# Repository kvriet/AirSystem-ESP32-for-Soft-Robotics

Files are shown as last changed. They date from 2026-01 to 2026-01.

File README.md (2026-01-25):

# AirSystem for Soft Robotics
Modular Air System for Soft Robotics using ESP32\
Designed and created by [C.M. van Riet](https://research.tue.nl/en/persons/cm-katrien-van-riet) - Jan 2026\
With thanks to d.search at Eindhoven University of Technology for their guidance.\
Special thanks to Geert van den Boomen for checking the schematics and debugging the circuits.

## The system
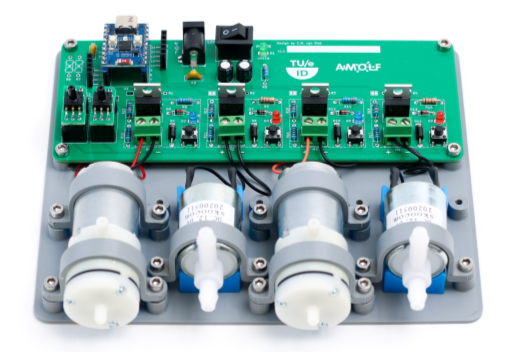
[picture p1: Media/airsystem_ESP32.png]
Example application


**AirSystem-ESP32** was designed as a low-cost way to rapidly prototype with air, costing roughly €60 for the entire system. AirSystem consists of 1 controller, 4 pneumatic components (pumps and valves), and 2 pressure sensors. Through a 12V power brick, the board provides 12V power and as such, any pump or solenoid that requires 12V power can be attached to the board. 

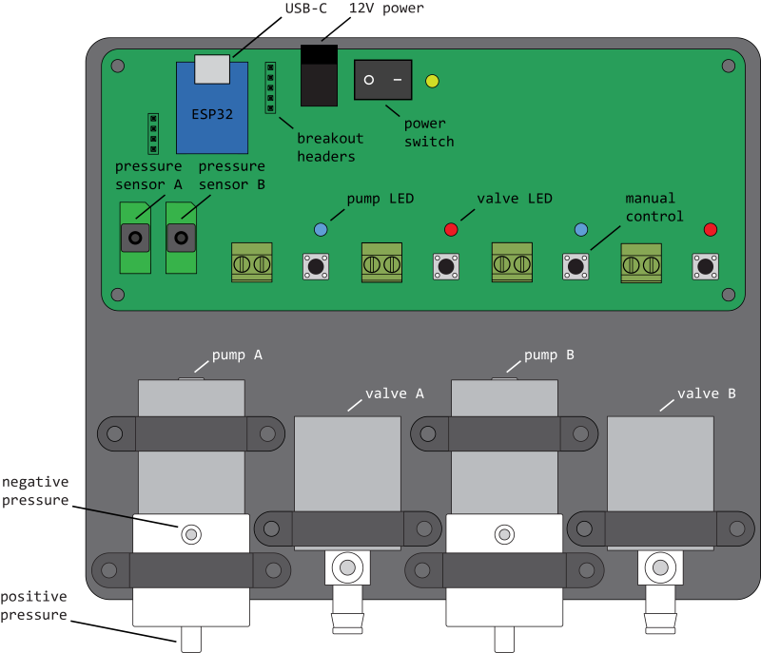
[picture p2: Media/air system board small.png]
System overview


### Pneumatic Components
For the pneumatic board, easy-to-find components are used:
1. Pump 370A, 12V, 3.2LPM
2. Solenoid valve Skoocom SC0829GW, 12V
3. MCP-H10 pressure sensor, 0-200kPa, 3.3V

### Manual
A manual for AirSystem describes in detail how the system works and how the Arduino library can be installed: [AirSystem Manual](https://github.com/kvriet/AirSystem-ESP32-for-Soft-Robotics/blob/main/Air%20System%20manual%20pcb%20v1.3.pdf)
Users are free to connect the sensor, pump, and valve to their inflatables as desired. Example Arduino sketches are provided that work well with the board to control inflatables.

## Arduino Library
The system is controlled by a Waveshare ESP32-C3-Zero and can be programmed through the Arduino IDE with a custom library: [AirSystem](https://github.com/kvriet/AirSystem-ESP32-for-Soft-Robotics/blob/main/AirSystem-ESP.zip) This folder should be unzipped and placed in the libraries folder of the Arduino folder, or imported (zipped) as a library in the Arduino IDE. Select the XIAO_ESP32C3 board to upload sketches to the board.

The library comes with 7 examples that showcase the abilities of **AirSystem**:
  1. Manual control
  2. Pressure reading
  3. Pump control
  4. Valve control
  5. Pump control without delay
  6. Other configurations
  7. Object arrays

## Schematics and KiCAD Files
The schematics for this project and the KiCAD files can be found here: [KiCAD folder](https://github.com/kvriet/AirSystem-for-Soft-Robotics/tree/main/KiCAD).

## 3D Printing Files
The STLs for this project can be found here: [Design Files](https://github.com/kvriet/AirSystem-ESP32-for-Soft-Robotics/tree/main/Design%20files).
- The prints will fit most regular printers and can be printed out of PLA, 0.3 layer height, 4 perimeters (walls), 20% infill. The cushions for the pumps and solenoids are printed in TPU. These cushions can be replaced with some sponge (simple kitchen sponges work well) if TPU printing is not an option.
- To minimise vibrations and prevent the cases from sliding around on a hard surface, 6mm silicone feet can be added to the bottom of the base.

The screws needed for these cases are:
- 4x M3x5 for the PCB 
- 12x M3x10 for the clamps (or 16x M3x10 depending on the configuration)

## Limitations
- The Skoocom solenoid valve is able to remain closed up to pressures of 100kPa, whereas the pump is able to deliver 150kPa. This means the valve will start leaking at pressures over 100kPa. In practice, this is not a major issue, as our projects rarely need pressures of over 100kPa (usually maxing out at 50kPa for haptic purposes). However, this overpressure might reduce valve longevity in the long run. In the future, a higher-pressure solenoid valve could be found, or a pump could be found that delivers max 100kPa. This would also allow for a lower-range pressure sensor to be used, the MCP-H10 0-100kPa, 3.3V. Switching to the 0-100kPa sensor would also double pressure measuring resolution.
- Currently no PID has been implemented in the library. As many inflatables or the tubing used are somewhat elastic, I have found that setting a target pressure (feedback loop sensor reading to pump power) is enough to achieve that pressure with a minimal offset. However, for more high-end applications, PID should be implemented.
- The Skoocom solenoid valve is not proportional. It is just open/closed. This means that controller deflation is a challenge. This can be worked around by turning on the pump simultaneously to opening the valve to reduce the air flowing out. Additionally, a resistor (very thin tube) could be connected to the valve outlet to reduce airflow out of the system. However, such a resistor also slows down response times when air does need to evacuate the system quickly. This is a trade-off for how cheap this entire system is.

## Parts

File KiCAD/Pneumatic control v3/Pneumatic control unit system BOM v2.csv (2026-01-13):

Reference | Value | Datasheet | Footprint | Qty | DNP | Katrien will provide
C1,C4,C5,C6,C7,C8 | 100nF | ~ | Capacitor_THT:C_Rect_L7.2mm_W2.5mm_P5.00mm_FKS2_FKP2_MKS2_MKP2 | 6 |  | no
C2,C3 | 100uF | ~ | Capacitor_THT:CP_Radial_D6.3mm_P2.50mm | 2 |  | no
D1,D7 | LED_Blue | ~ | LED_THT:LED_D3.0mm | 2 |  | no
D2,D8 | LED_Red | ~ | LED_THT:LED_D3.0mm | 2 |  | no
D3,D4,D9,D10 | 1N4001 | http://www.vishay.com/docs/88503/1n4001.pdf | Diode_THT:D_DO-41_SOD81_P10.16mm_Horizontal | 4 |  | no
D5,D6,D11,D12 | 1N4148 | https://assets.nexperia.com/documents/data-sheet/1N4148_1N4448.pdf | Diode_THT:D_DO-35_SOD27_P7.62mm_Horizontal | 4 |  | no
D13 | LED_Small | ~ | LED_THT:LED_D3.0mm | 1 |  | no
J1 | Barrel_Jack | https://www.tinytronics.nl/en/cables-and-connectors/connectors/dc-jack/dc-jack-plastic-5.5mm-female | Connector_BarrelJack:BarrelJack_Horizontal | 1 |  | yes
J2,J3 | Conn | ~ | -- mixed values -- | 2 |  | no
J4 | GND | ~ | TestPoint:TestPoint_Loop_D2.50mm_Drill1.0mm | 1 | DNP | no
JP1,JP2,JP3,JP4,JP5,JP6 | jumper | ~ | Jumper:SolderJumper-2_P1.3mm_Bridged_Pad1.0x1.5mm | 6 |  | no
M1,M3 | Pump | ~ | TerminalBlock_Phoenix:TerminalBlock_Phoenix_MKDS-1,5-2_1x02_P5.00mm_Horizontal | 2 |  | yes
M2,M4 | Valve | ~ | TerminalBlock_Phoenix:TerminalBlock_Phoenix_MKDS-1,5-2_1x02_P5.00mm_Horizontal | 2 |  | yes
Q1,Q2,Q3,Q4 | IRLB8743PBF | https://www.infineon.com/assets/row/public/documents/24/49/infineon-irlr8743-datasheet-en.pdf | Package_TO_SOT_THT:TO-220-3_Vertical | 4 |  | no
R1,R2,R3,R4 | 1k | ~ | Resistor_THT:R_Axial_DIN0207_L6.3mm_D2.5mm_P10.16mm_Horizontal | 4 | DNP | no
R5,R11,R17 | 3k3 | ~ | Resistor_THT:R_Axial_DIN0207_L6.3mm_D2.5mm_P10.16mm_Horizontal | 3 |  | no
R6,R12 | 1k2 | ~ | Resistor_THT:R_Axial_DIN0207_L6.3mm_D2.5mm_P10.16mm_Horizontal | 2 |  | no
R7,R8,R13,R14 | 1k | ~ | Resistor_THT:R_Axial_DIN0207_L6.3mm_D2.5mm_P10.16mm_Horizontal | 4 |  | no
R9,R10,R15,R16 | 100k | ~ | Resistor_THT:R_Axial_DIN0207_L6.3mm_D2.5mm_P10.16mm_Horizontal | 4 |  | no
SW1 | SW_SPST | https://www.tinytronics.nl/en/switches/manual-switches/rocker-switches/standaard-built-in-rocker-switch-small | Library:SW_rocker_switch_small | 1 |  | yes
SW2,SW3,SW4,SW5 | SW_Push | ~ | Button_Switch_THT:SW_PUSH_6mm | 4 |  | no
U1,U2 | ~ |  | Library:MCP_H10_breakout | 2 |  | yes
U3 | ESP32-C3-Zero |  | ESP32-C3-Zero | 1 |  | yes

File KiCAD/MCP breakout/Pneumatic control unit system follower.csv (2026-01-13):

Reference | Value | Datasheet | Footprint | Qty | DNP
C1,C2,C3,C4,C7,C8,C11 | 100nF | ~ | Capacitor_SMD:C_0603_1608Metric_Pad1.08x0.95mm_HandSolder | 7
C5,C6,C9,C10 | 100uF | ~ | Capacitor_THT:CP_Radial_D6.3mm_P2.50mm | 4
D1,D3 | LED_Small | ~ | Diode_SMD:D_0805_2012Metric_Pad1.15x1.40mm_HandSolder | 2
D2,D4 | 1N4007 | http://www.vishay.com/docs/88503/1n4001.pdf | Diode_SMD:D_SMA_Handsoldering | 2
D5,D6 | 1N4148 | https://assets.nexperia.com/documents/data-sheet/1N4148_1N4448.pdf | Diode_SMD:D_MiniMELF_Handsoldering | 2
J1 | unit_1 | https://www.tinytronics.nl/en/cables-and-connectors/connectors/jst-compatible/jst-xh-6p-compatible-pcb-connector-male-90 | Library:JST_XH_S6B-XH-A-1_1x06_P2.50mm_Horizontal_5mm | 1
M1,M2 | Pump | ~ | TerminalBlock_Phoenix:TerminalBlock_Phoenix_MPT-0,5-2-2.54_1x02_P2.54mm_Horizontal | 2
Q1,Q2 | AO3400A | http://www.aosmd.com/pdfs/datasheet/AO3400A.pdf | Package_TO_SOT_SMD:SOT-23 | 2
R1,R4 | 680R | ~ | Resistor_SMD:R_0603_1608Metric_Pad0.98x0.95mm_HandSolder | 2
R2,R5 | 330R | ~ | Resistor_SMD:R_0603_1608Metric_Pad0.98x0.95mm_HandSolder | 2
R3,R6 | 100k | ~ | Resistor_SMD:R_0603_1608Metric_Pad0.98x0.95mm_HandSolder | 2
SW1,SW2 | SW_Push | ~ | Button_Switch_THT:SW_PUSH_6mm | 2
U1 | ~ |  | Library:MCP-H10 | 1

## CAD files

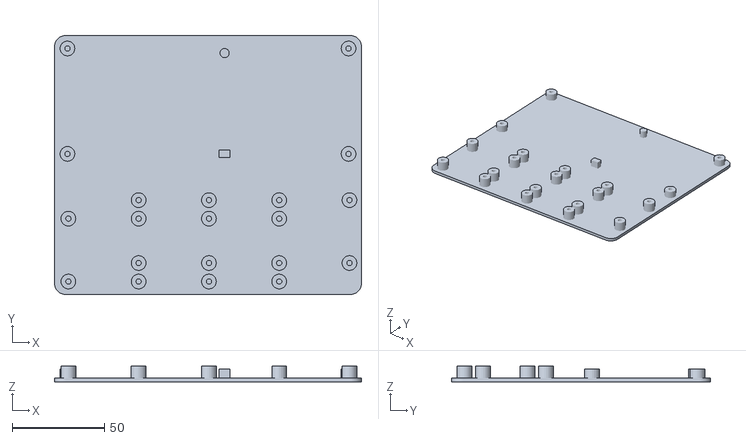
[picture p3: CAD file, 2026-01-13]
Design files/pcb base v2.stl
166.0 x 140.0 x 8.50

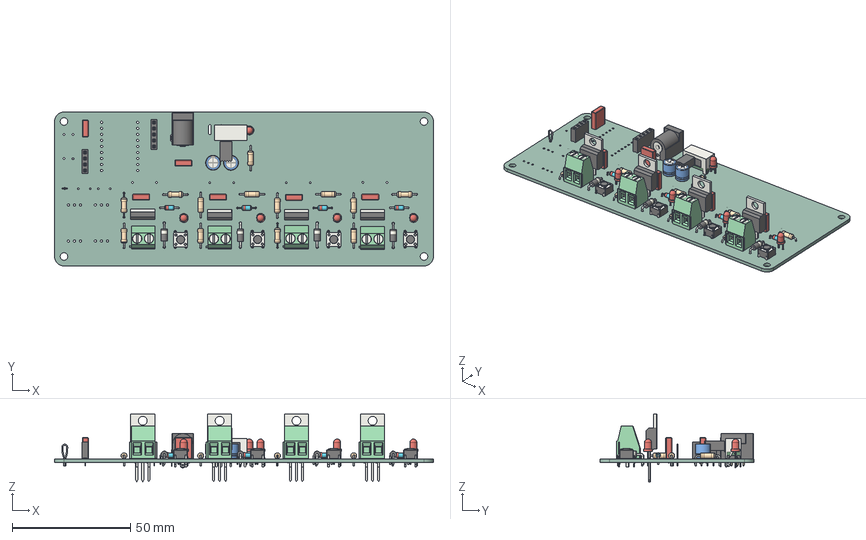
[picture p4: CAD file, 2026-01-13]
KiCAD/Pneumatic control v3/control unit v3.step
160.0 x 65.0 x 28.5 mm
C_Rect_L72mm_W25mm_P500mm_FKS2_FKP2_MKS2_MKP2 x 6
R_Axial_DIN0207_L63mm_D25mm_P1016mm_Horizontal x 13
LED_D3.0mm x 5
SW_PUSH_6mm x 4
PinSocket_1x04_P254mm_Vertical
D_DO-41_SOD81_P10.16mm_Horizontal x 4
TO-220-3_Vertical x 4
PinSocket_1x05_P254mm_Vertical
TerminalBlock_Phoenix_MKDS_15_2_1x02_P500mm_Horizontal x 4
D_DO-35_SOD27_P7.62mm_Horizontal x 4
CP_Radial_D63mm_P250mm x 2
SW_E-Switch_EG1224_SPDT_Angled
BarrelJack_Horizontal
TestPoint_Loop_D2.50mm_Drill1.0mm
Pneumatic control unit system_PCB

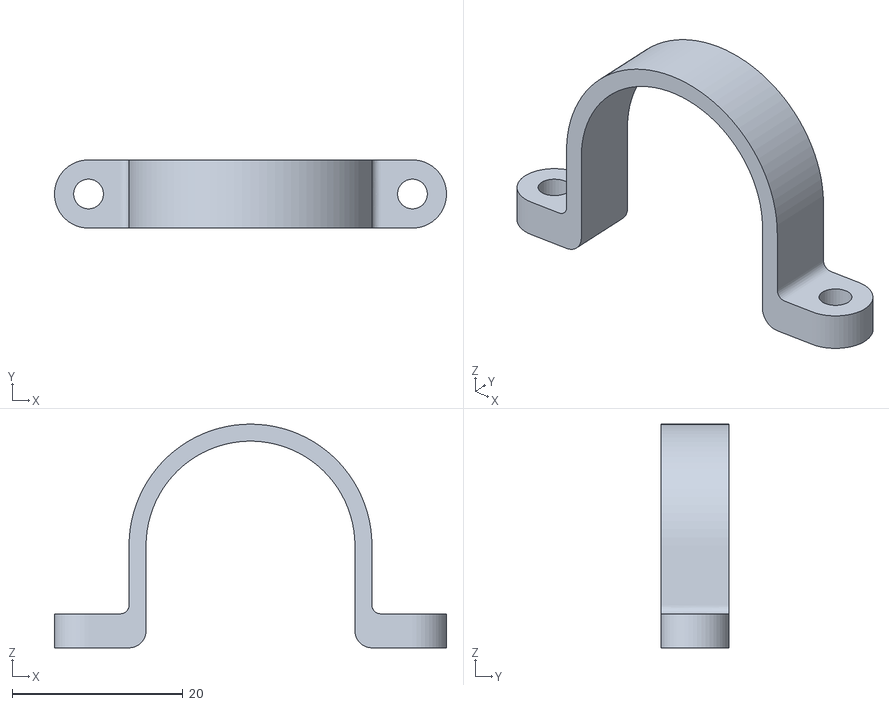
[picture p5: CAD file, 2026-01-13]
Design files/clamp small v5.stl
46.0 x 8.00 x 26.2

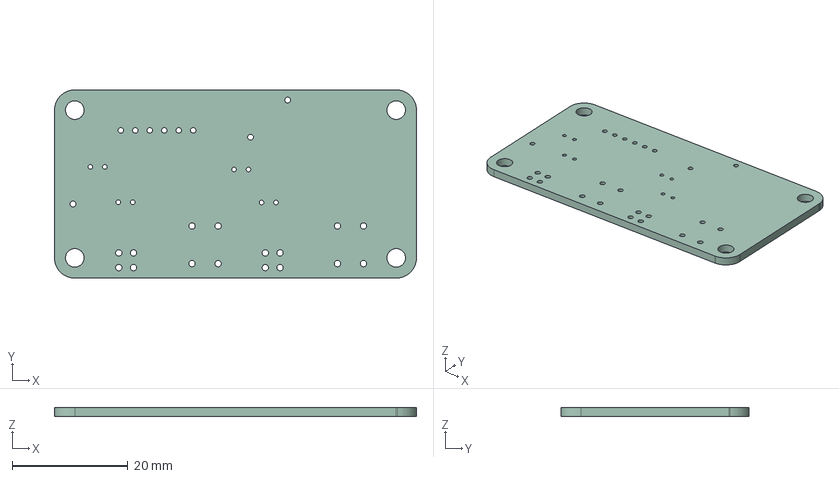
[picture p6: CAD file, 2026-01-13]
KiCAD/MCP breakout/Pneumatic control unit system broad.step
62.5 x 32.5 x 1.60 mm

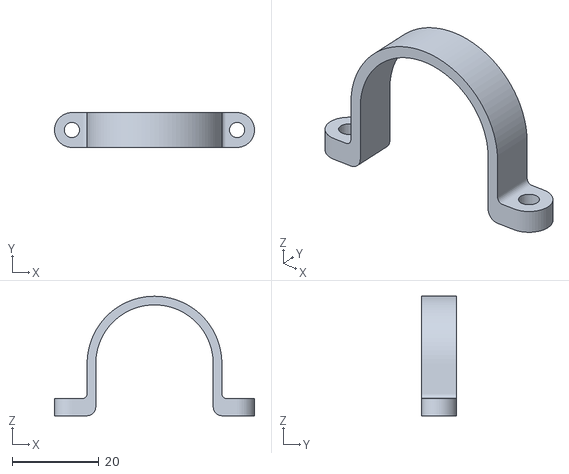
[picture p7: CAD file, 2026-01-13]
Design files/clamp big v5.stl
46.0 x 8.00 x 27.5

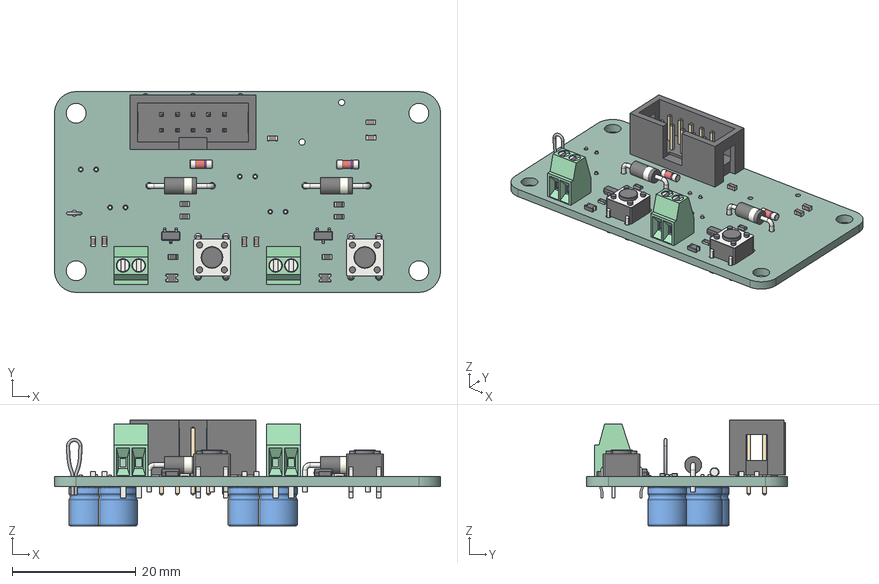
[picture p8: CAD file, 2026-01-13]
KiCAD/MCP breakout/follower v8.2.step
62.5 x 32.5 x 17.1 mm
R_0603_1608Metric x 6
D_MiniMELF_Standard x 2
D_DO-41_SOD81_P10.16mm_Horizontal x 2
SW_PUSH_6mm x 2
TestPoint_Loop_D2.50mm_Drill1.0mm
C_0603_1608Metric x 7
IDC_Header_2x05_P254mm_Vertical
TerminalBlock_Phoenix_MPT_05_2_254_1x02_P254mm_Horizontal x 2
SOT_23 x 2
D_0805 x 2
CP_Radial_D63mm_P250mm x 4
Pneumatic control unit system_PCB

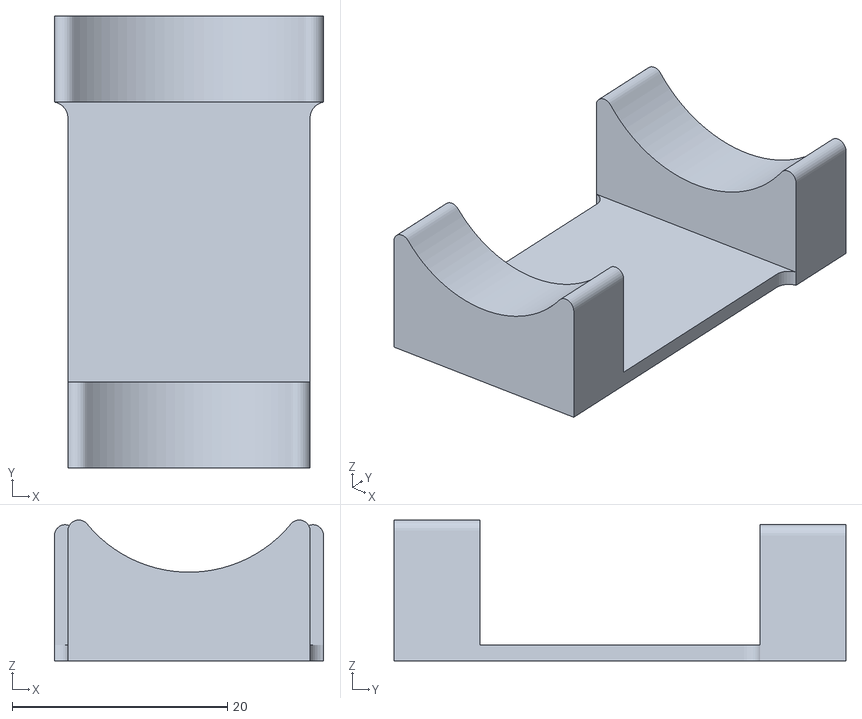
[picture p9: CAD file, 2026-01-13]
Design files/cushion connected v3.stl
25.0 x 42.0 x 13.1

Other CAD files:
KiCAD/MCP breakout/follower v8.step

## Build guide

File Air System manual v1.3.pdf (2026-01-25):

# AIR CONTROL SYSTEM

# MANUAL

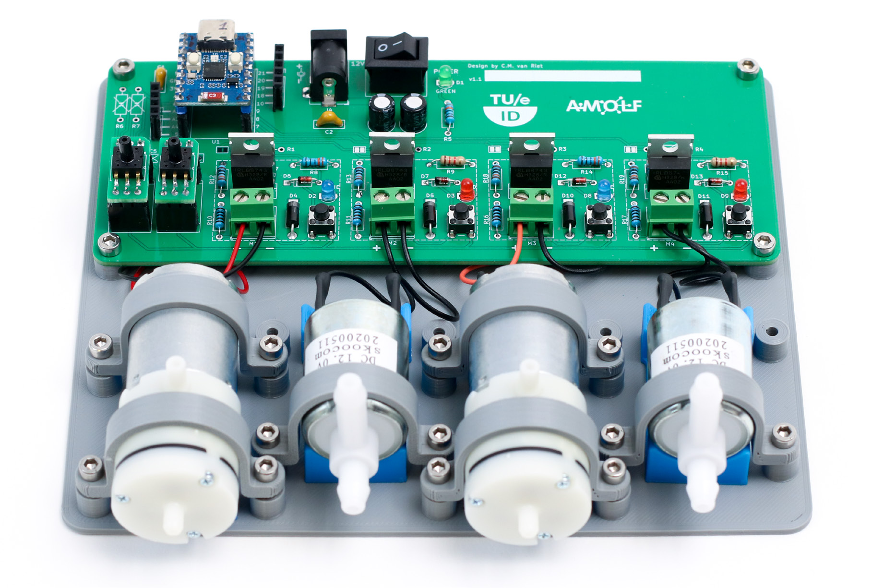
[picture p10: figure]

C.M. van Riet - January '26 - v1.3

# OVERVIEW

The Air Control System controls up to 4 pumps or valves. It is powered by a 12V power supply and an ESP32 C3 Zero, which can be programmed through the Arduino IDE.

In its standard configuration, each Air System contains two pumps, two solenoid valves, and two pressure sensors:

- The pump can provide positive and negative pressure (vacuum). You will mainly use positive pressure.
- The valve is normally closed. Activating the valve opens it.
- The pump and valve can be manually turned on by pressing the buttons.
- The LEDs indicate whether the pump or valve are turned on.

The pumps and valves can be replaced. In this way, the board can support any configuration of pumps and valves.

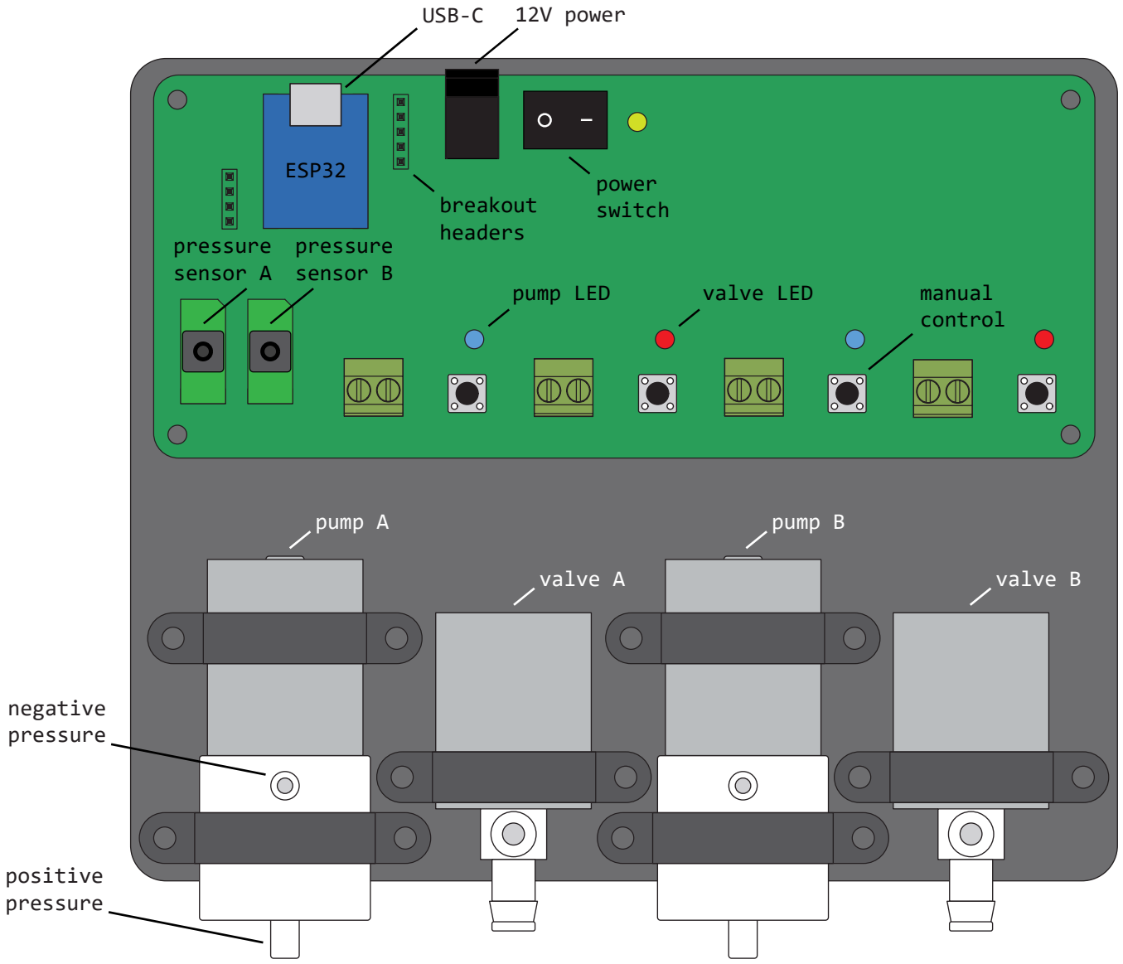
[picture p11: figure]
power switch; USB-C 12V power; manual control; pump LED; valve LED; ESP32; breakout headers; negative pressure; positive pressure; pump A; valve A; pump B; valve B; pressure sensor A; pressure sensor B

# POUCH CONNECTION

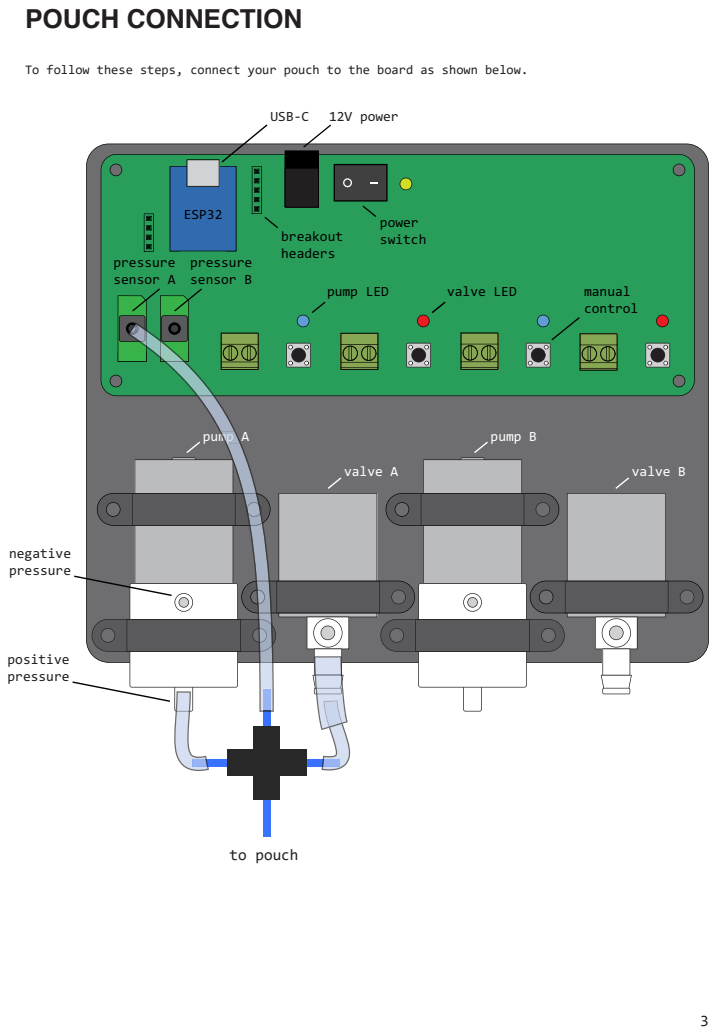
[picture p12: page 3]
power switch; USB-C 12V power; manual control; pump LED; valve LED; ESP32; breakout headers; negative pressure; positive pressure; pump A; valve A; pump B; valve B; pressure sensor A; pressure sensor B; to pouch

To follow these steps, connect your pouch to the board as shown below.

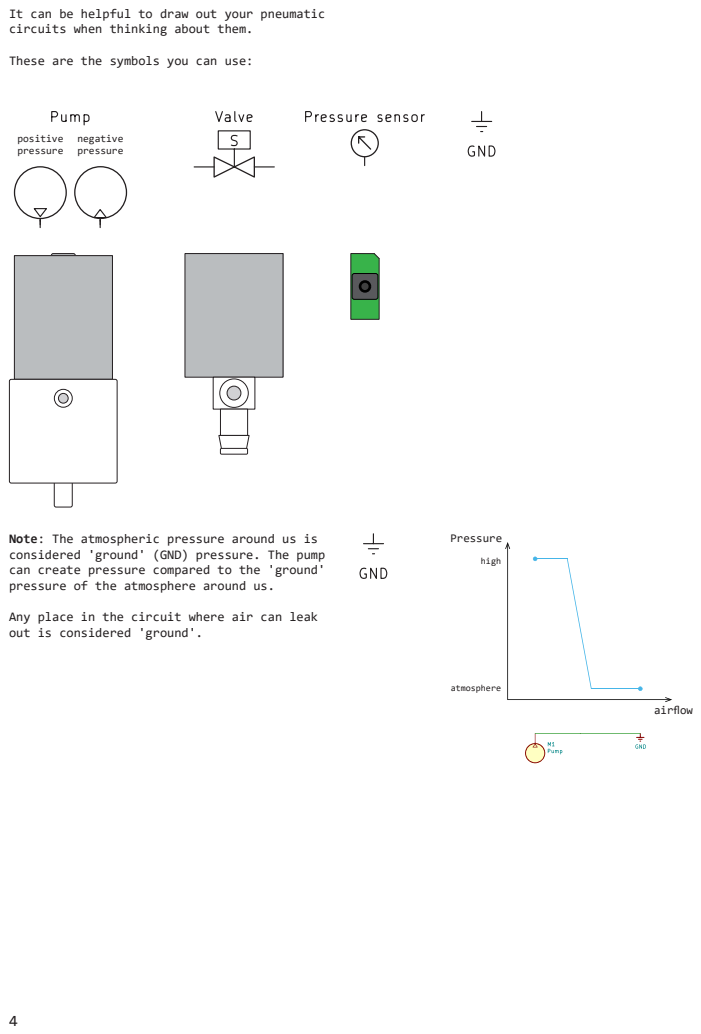
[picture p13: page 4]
positive pressure; negative pressure; Pressure; high; atmosphere; airflow

It can be helpful to draw out your pneumatic
circuits when thinking about them.
These are the symbols you can use:

Note: The atmospheric pressure around us is
considered 'ground' (GND) pressure. The pump
can create pressure compared to the 'ground'
pressure of the atmosphere around us.
Any place in the circuit where air can leak
out is considered 'ground'.

# INSTALLING THE ARDUINO LIBRARY

Before you can make Arduino sketches using the AirSystem library, you need to install the library.

To do this, import the AirSystem-ESP folder (zipped) into your Arduino IDE.
You can download the zipped library here: https://github.com/kvriet/AirSystem-ESP32-for-Soft-Robotics/blob/main/AirSystem-ESP.zip

To install the library, start the Arduino IDE. Go to:
Sketch > Include Library > Add .ZIP Library.
Select the zipped library folder and click 'open'. The Airsystem library should now be installed.

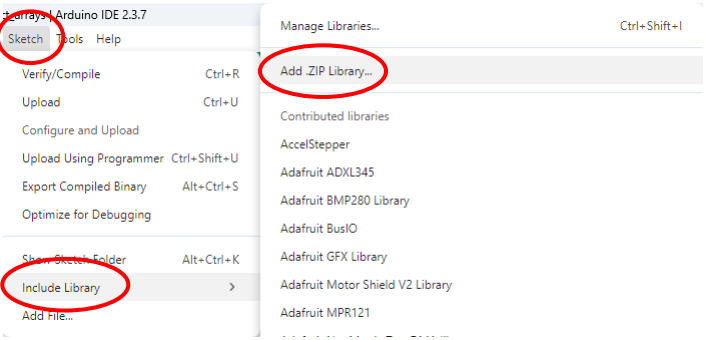
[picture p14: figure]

If everything went well, your Arduino library structure should look as follows:

Arduino/
└── libraries/
└── AirSystem-ESP/
├── AirSystem-ESP.h
├── AirSystem-ESP.cpp
└── examples/

Whenever you want to use the library, don't forget to call it at the top of your sketch: #include <AirSystem-ESP.h>

Also don't forget to initialise the pins in the setup loop:
AirSystem_begin(); // Initialise the pins

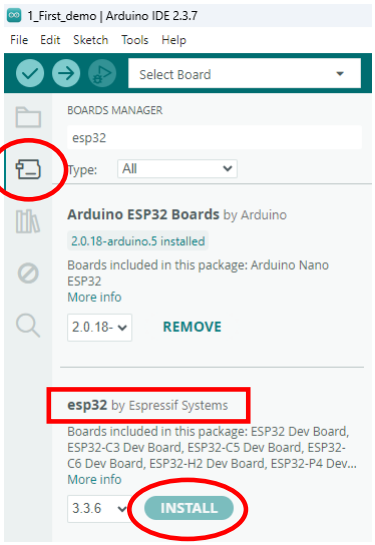
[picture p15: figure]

4. Click the USB connection drop-down menu (circled in red) Click 'Select other board and port...'

Search for 'XIAO ESP32 C3'

Select 'XIAO_ESP32C3' and click the correct port on the right of the menu.

You are now done and able to upload sketches to the ESP32!

# INSTALLING THE ESP32 BOARD

1. Connect the ESP32 to your computer.
2. In the Arduino IDE, go to File > Preferences...
In the 'Additional boards manager URLs' box, paste this URL:
https://raw.githubusercontent.com/espressif/arduino-esp32/gh-pages/package_esp32_index. json
3. Click the board library. Search for 'ESP32'. Install the ESP32 Espressif board library. This will take a moment.

# PROGRAMMING

The AirSystem library is an object-oriented library that provides three types of objects:
- Pump → controls an air pump using PWM (0–100% power).
- Valve → controls a solenoid valve (open/close).
- Sensor → reads air pressure from a pressure sensor.
Accessing Objects
You can access objects in two ways:
By name (if you created them individually):
- PumpA.set(50); | // Set PumpA to 50% power
- ValveB.open(); | // Open ValveB
- float p = SensorA.read(); // Read SensorC pressure

By array index:
- motors[0].set(50); | // PumpA
- motors[1].on(); | // ValveB
- motors[2].off(); | // PumpB
Functions
Pump/Motor
- set(percentage) → Set pump power (0–100%).
- off() | → Turn pump off (same as set(0)).
- on() | → Turn pump fully on (100%).

Valve
- open() | → Open the valve.
- close() | → Close the valve.

Sensor
- read() | → Returns the current pressure in kPa (kiloPascal).

# STEP 1: MANUAL CONTROL

(All these steps are also included as examples in the Airsystem library.)

The pump and valves can be operated through the push buttons on the follower unit.

Upload the following code. It will not activate the pumps or valves. Instead you can press the pump and valve buttons to inflate and deflate your pneumatic button.

Turn on the Airsystem with the power switch. The green LED should light up.
If you quickly want to deactivate your pumps and valves, you can always switch off the power.

/*
AirSystem Demo Sketch

Author: C.M. van Riet
Library: AirSystem-ESP
Date: January 2026

Objects can be called in 3 ways:
- pumpA, valveB, sensorA (named)
- M1, M2, M3, M4 (named)
- pumps[0], valves[1], sensors[0] (array-based)

Functions available in this library:
- Initialize the system with AirSystem_begin()
- Control pumps with .set(percentage), on(), and .off()
- Control valves with .open() and .close()
- Read pressure from sensors with .read()

Hardware:
- Designed for a maximum of 4 pumps or 4 valves, and 2 sensors
- Pin mappings are fixed in the library (see AirSystem-ESP.h)

Notes:
- Make sure to include the AirSystem-ESP.h library at the top of your sketch (#include <AirSystem-ESP.h>)
- This example can be found under File > Examples > AirSystem-ESP > 1_First_demo. */

#include <AirSystem-ESP.h>

void setup() {
Serial.begin(9600);
AirSystem_begin(); // Initialise the pins
pumpA.off(); | // Pump off
valveA.close(); | // Close valve
pumpB.off(); | // Pump off
valveB.close(); | // Close valve
}

void loop() {
// This loop is empty
// You can turn on the pump and valve by pressing // the buttons on the Air System board
}

#include <AirSystem-ESP.h>

void setup() {
Serial.begin(9600);
AirSystem_begin(); // Initialise the pins
pumpA.off(); | // Pump off
valveA.close(); | // Close valve
pumpB.off(); | // Pump off
valveB.close(); | // Close valve
}

void loop() {
float pressure = sensorA.read();
Serial.print(0); // Lower limit in Serial Plotter Serial.print("\t"); // Print a tab Serial.print(200); // Upper limit in Serial Plotter Serial.print("\t"); // Print a tab Serial.println(pressure);

delay(10);
}

# STEP 2: PRESSURE READINGS

To get the pressure sensor value, use the read() function. The pressure is in kPa.

Upload the following code. Use the push buttons to inflate and deflate your pouch and use the Serial Monitor and Serial Plotter (top right of IDE) to watch the pressure value fluctuate.

# STEP 3: PUMP CONTROL

The code below turns the pump on and off.

- Try to change the delay values. How does the pump turning on and off change?
- Try to change the value in the set() function. How does it change the pump behaviour?
- When not activated, does the pump allow air to leak out?

#include <AirSystem-ESP.h>

void setup() {
Serial.begin(9600);
AirSystem_begin(); // Initialise the pins
pumpA.off(); | // Pump off
valveA.close(); | // Close valve
pumpB.off(); | // Pump off
valveB.close(); | // Close valve
}

void loop() {
pumpA.set(50);
Serial.println("Pump set to 50% intensity");

delay(2000);

pumpA.off();
Serial.println("Pump turned off");

delay(2000);
}

#include <AirSystem-ESP.h>

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

void loop() {
valveA.close();
pumpA.set(25);
Serial.println("Valve closed and pump set to 25%");

delay(1000);

valveA.open();
pumpA.off();
Serial.println("Valve opened and pump turned off");

delay(2000);
}

# STEP 4: VALVE CONTROL

The code below is similar to the code in step 3, but it adds valve control. Now you can inflate and deflate your pouch. Above 100kPa, the solenoid valve will release air, but not break.

- Play with the pump power percentage and the timing (delay) to get an aesthetically pleasing inflation and deflation of your pouch.

# STEP 5: PUMP WITHOUT DELAY

In step 4 we turned the pump on and off. We used the delay() function for this, but this freezes up the entire program; you can't do anything else during the delay. To fix this, the code below gives pump control without delay, similar to the 'Blink without delay' example in the Arduino library. For this to work, we use a general timer (currentMillis) to keep track of time.

// Pump without delay based on the code by David A. Mellis

#include <AirSystem-ESP.h>

// Variables will change:
int pumpState = LOW; // pumpState used to set the pump on/off

// Generally, you should use "unsigned long" for variables that hold time
// The value will quickly become too large for an int to store
unsigned long previousMillis = 0; // will store last time pump state was updated

// Constants won't change:
const long interval = 1000; // interval at which to blink (milliseconds)
// Blink here means turn the pump on and off

#include <AirSystem-ESP.h>

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

void loop() {
// Here is where you'd put code that needs to be running all the time.

// Get the current elapsed milliseconds from the start of the sketch
unsigned long currentMillis = millis();

if (currentMillis - previousMillis >= interval) {
// This if-statement checks if the current time is bigger than the previous time - interval // So check if the interval time (1 second) has elapsed
previousMillis = currentMillis;
// If the pump is off, turn it on and vice-versa:
if (pumpState == LOW) {
pumpState = HIGH;
pumpA.set(50); // Set pump to 50% valveA.close(); // Close valve
} else {
pumpState = LOW;
pumpA.off(); // Turn pump off valveA.open(); // Open valve }
}
Serial.print(currentMillis); Serial.print("\t");
Serial.print(previousMillis); Serial.print("\t");
Serial.printn(interval);
}

# STEP 6: OTHER CONFIGURATIONS

In the previous examples, we assumed that the board layout contained 2 pumps and 2 valves in a pump, valve, pump, valve configuration. However, if you want to use different configurations, we need more generic names to call these components. For this we use the 'motor' designation: M1, M2, M3, M4. This does not affect how the sensors are called.
Because Arduino does not know what type of component it is addressing, control functions are limited to .set(percentage), on(), and .off()

#include <AirSystem-ESP.h>

void setup() {
Serial.begin(9600);
AirSystem_begin(); // Initialise the pins
M1.off(); | // Component 1 off
M2.off(); | // Component 2 off
M3.off(); | // Component 3 off
M4.off(); | // Component 4 off
}

void loop() {
// Set component 3 to 25% (this is pump B) and component 4 to 10% (this is valve B) M3.set(25);
M4.set(10); // Notice that at 10%, valve B does not open!
delay(1000);

// Set component 3 to 0% and component 4 to 50% M3.set(0);
M4.set(50); // Notice that at 50%, valve B does open! delay(1000);

float pressure = sensorA.read(); // Calling sensors remains unaffected Serial.println(pressure);
}

# STEP 7: OBJECT ARRAYS

In the previous examples we worked with named objects for the pump and valve. However, you can also directly address these objects within they object array. This can be useful if you want to loop through the objects. The code below shows you how to access pumps and valves through motors[i].

#include <AirSystem-ESP.h>

int motorPercentage = 0;

void setup() {
Serial.begin(9600);
AirSystem_begin(); // Initialise the pins for (int i = 0; i < 4; i++) {
// Turn off all components motors[i].off();
}
}

void loop() {
motors[0].set(motorPercentage); // pump A motors[1].set(motorPercentage); // valve A

motorPercentage++; // Add 1 to the motorPercentage variable

if (currentMillis > 100) {
motorPercentage = 0; // If motorPercentage becomes larger than 100, make it 0 again }

delay(100);
}

PumpA = 6
PumpB = 8

ValveA = 7
ValveB = 9

SensorA = 0
SensorB = 1

LED_BUILTIN = 10 (WS2812, RGB)

# PIN OVERVIEW (STANDARD CONFIGURATION)

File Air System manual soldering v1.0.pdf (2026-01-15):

# AIR CONTROL SYSTEM

# SOLDERING MANUAL

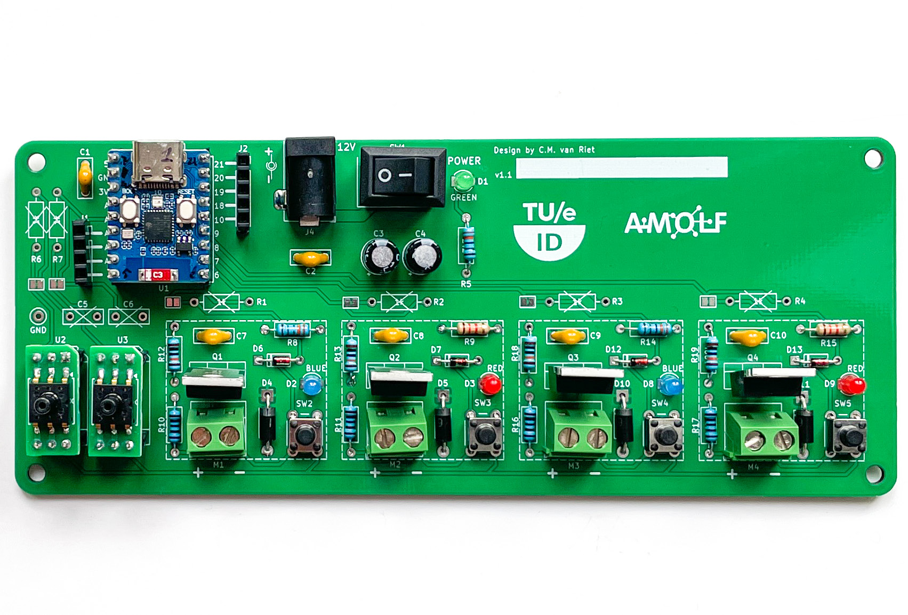
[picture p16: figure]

C.M. van Riet - January '26 - v1.0

# COMPONENTS

1. Resistors: 1k, 1k2, 3k3, 100k
2. Diodes: 1N4001, 1N4148
3. Unpolarised capacitors (ceramic): 100nF
4. Push buttons
5. LEDs 3mm
6. Headers
7. Polarised capacitors (electrolytic): 100uF
8. DC jack
9. Power switch
10. Terminals
11. Mosfets: IRLB8743

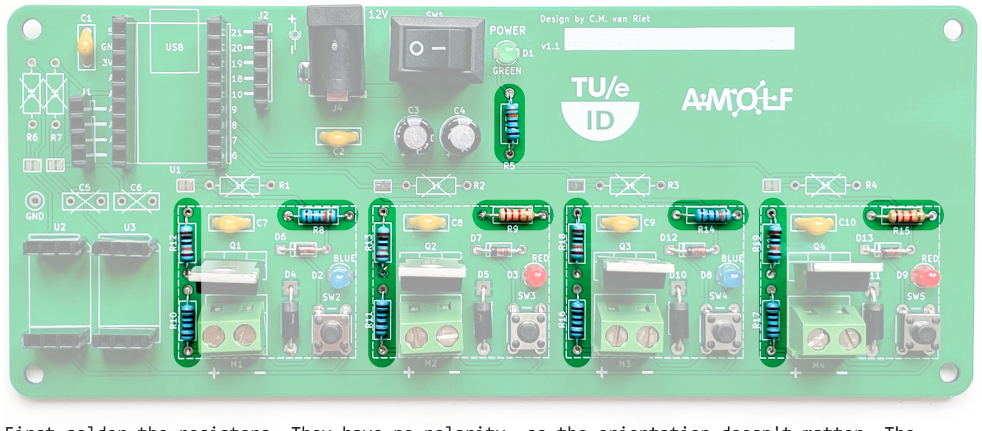
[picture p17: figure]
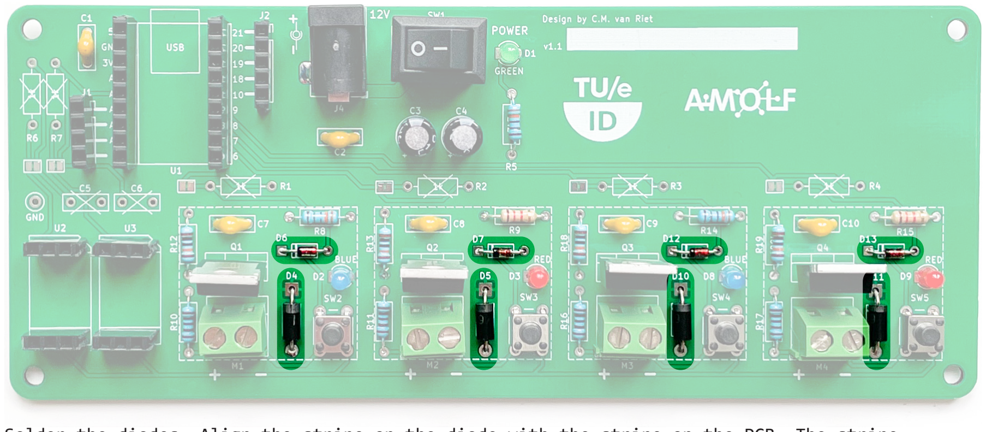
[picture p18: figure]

Solder the diodes. Align the stripe on the diode with the stripe on the PCB. The stripe indicates the cathode (negative side) of the diode.
_ +

# STEP 1: RESISTORS

First solder the resistors. They have no polarity, so the orientation doesn't matter. The resistor values are indicated on the PCB. These are the colour codes on the resistors themselves (for 5-band resistors):

1k | 3k3
1k2 | 100k

# STEP 2: DIODES

# STEP 3: UNPOLARISED CAPACITORS

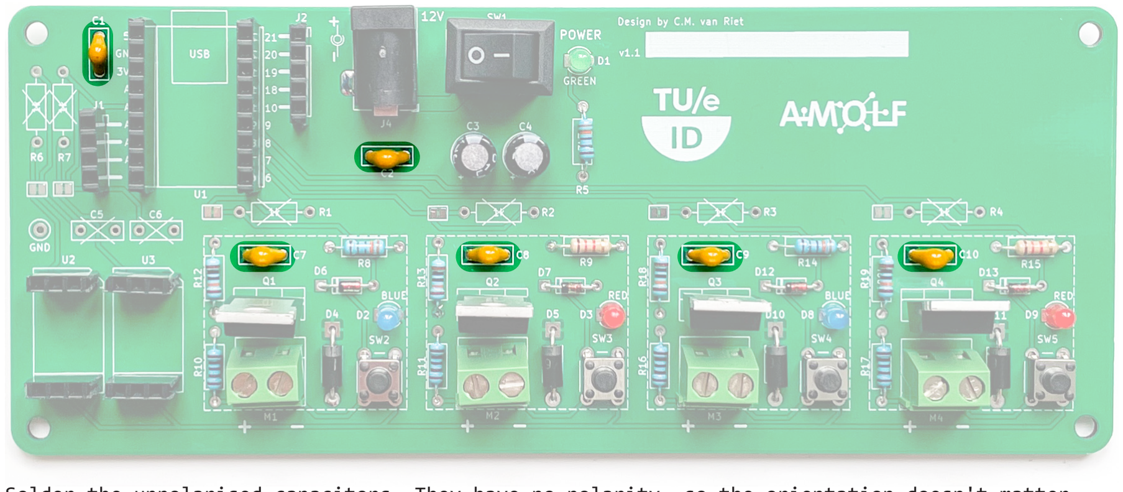
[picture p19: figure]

# STEP 4: PUSH BUTTONS

Solder the unpolarised capacitors. They have no polarity, so the orientation doesn't matter.

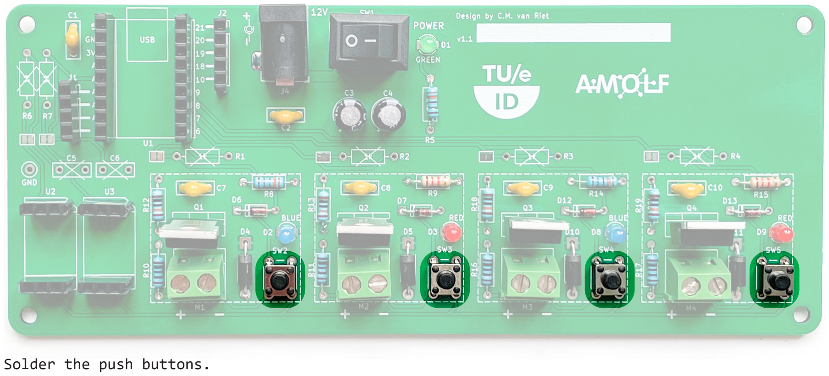
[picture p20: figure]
Solder the push buttons.

# STEP 5: LEDS

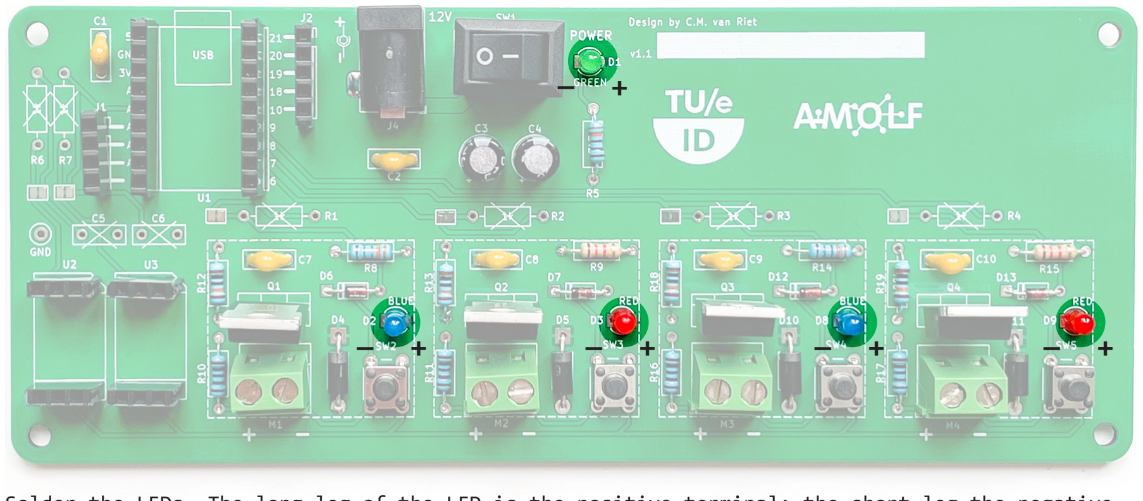
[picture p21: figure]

# STEP 6: HEADERS

Solder the LEDs. The long leg of the LED is the positive terminal; the short leg the negative terminal. You can also see the polarity from the top of the LED. The flat side is the negative side.
_ +

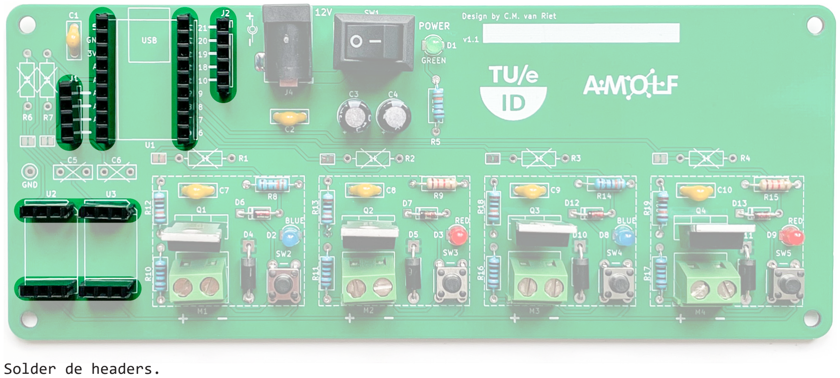
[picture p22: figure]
Solder de headers.

# STEP 7: POLARISED CAPACITOR

# STEP 8: DC JACK

Solder the polarised capacitor. The short leg is the negative terminal; the long leg is the positive terminal. The white stripe also indicates the negative terminal.
Align the positive side with the + sign on the PCB.

Solder the DC jack. The leads are quite big, so use enough solder and take some time.

_

+

_

+

# STEP 9: POWER SWITCH

# STEP 10: TERMINALS

Solder the power switch. The leads are quite big, so use enough solder and take some time.

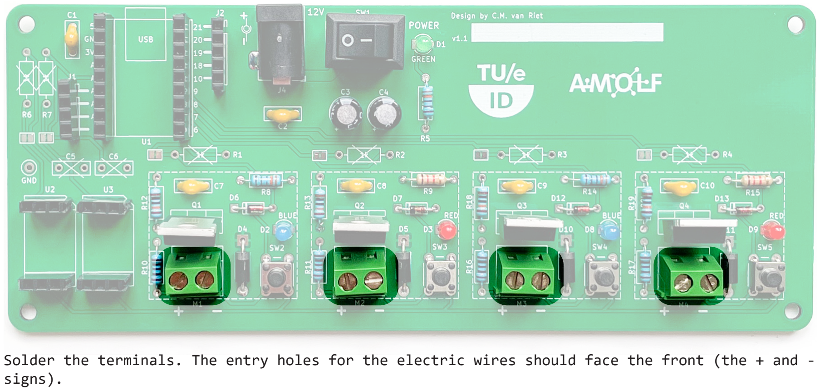
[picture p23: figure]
signs).

Solder the terminals. The entry holes for the electric wires should face the front (the + and -

# STEP 11: MOSFET

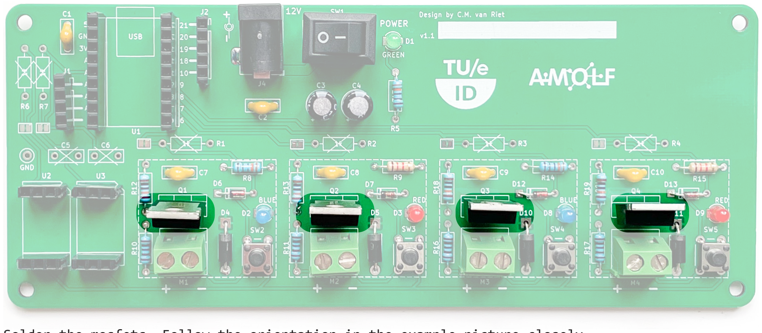
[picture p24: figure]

# STEP 12: INSPECTION

Solder the mosfets. Follow the orientation in the example picture closely.

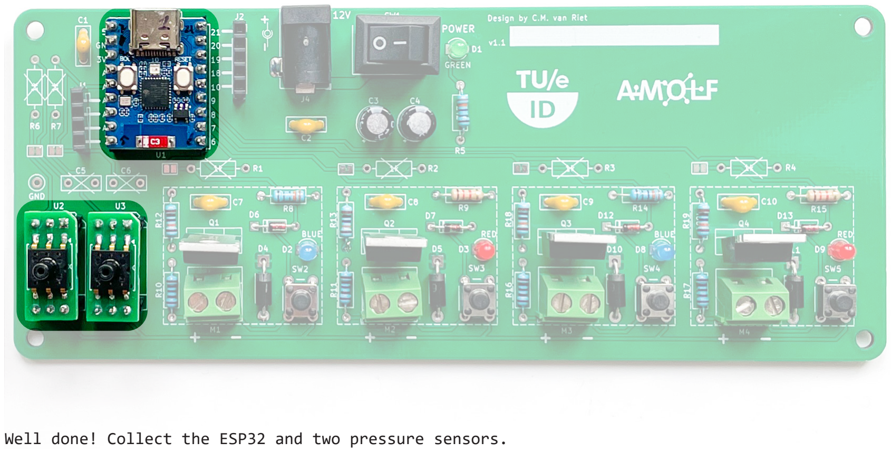
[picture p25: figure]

Well done! Collect the ESP32 and two pressure sensors.

# STEP 13: CASE

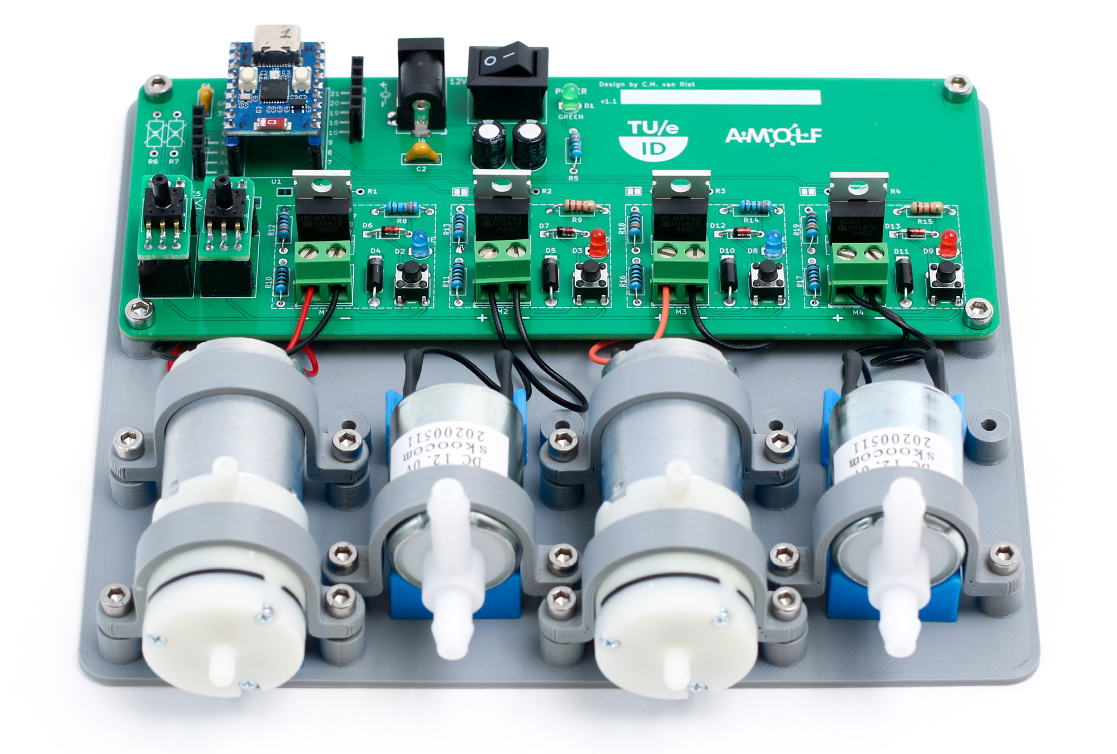
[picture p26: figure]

Collect the pumps, valves, PCB case, clamps, cushions, and screws.

Assemble the case as seen above.

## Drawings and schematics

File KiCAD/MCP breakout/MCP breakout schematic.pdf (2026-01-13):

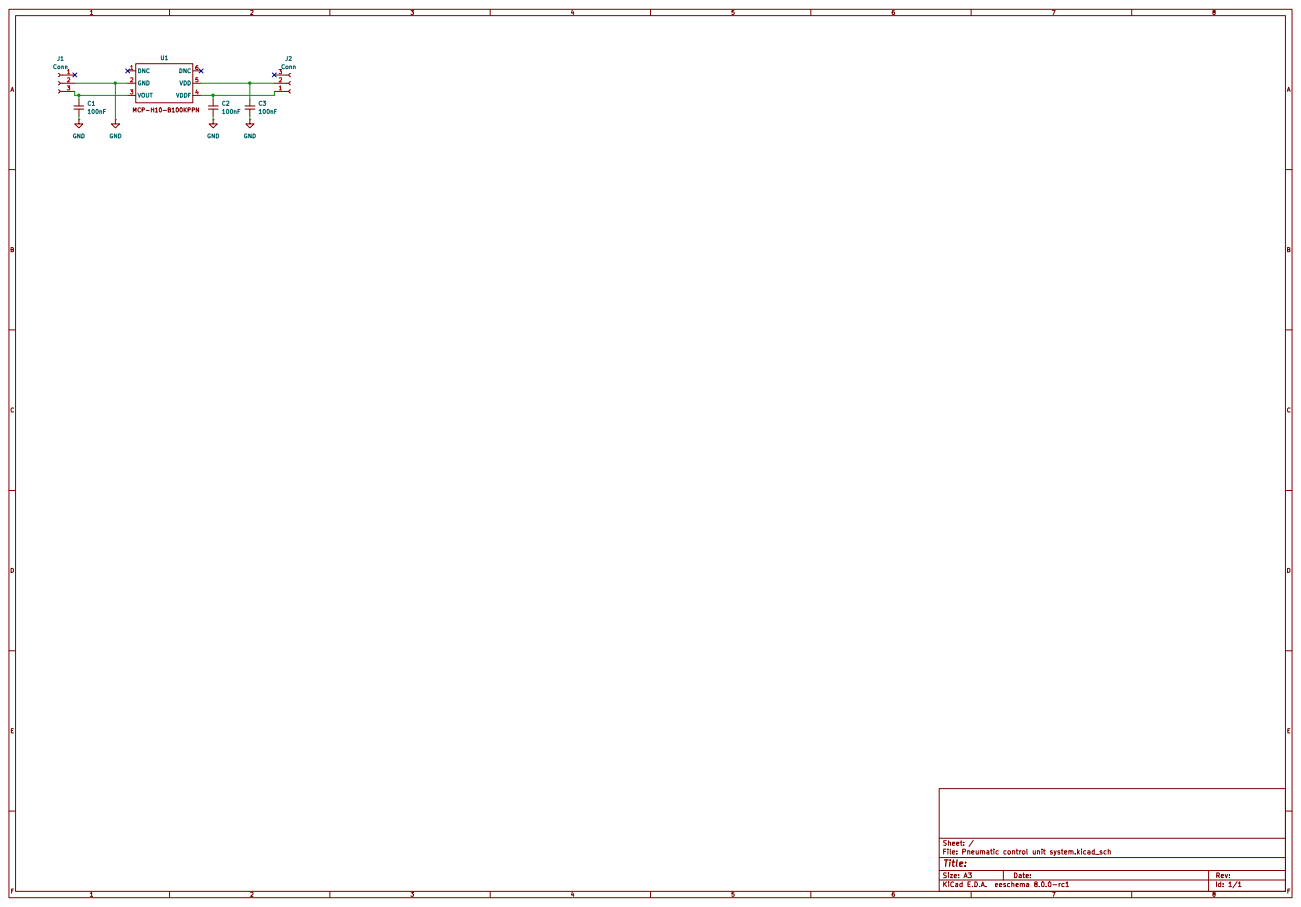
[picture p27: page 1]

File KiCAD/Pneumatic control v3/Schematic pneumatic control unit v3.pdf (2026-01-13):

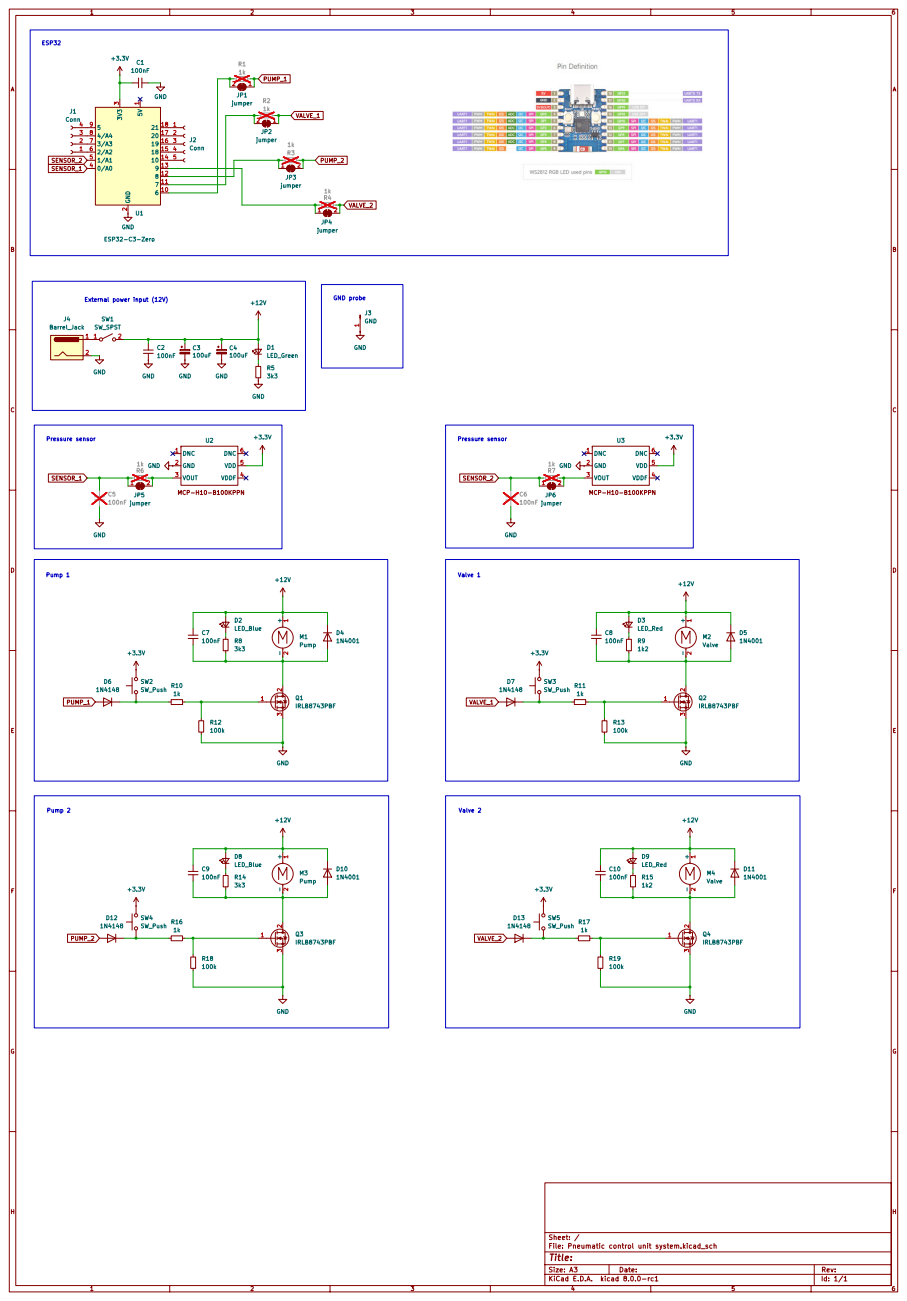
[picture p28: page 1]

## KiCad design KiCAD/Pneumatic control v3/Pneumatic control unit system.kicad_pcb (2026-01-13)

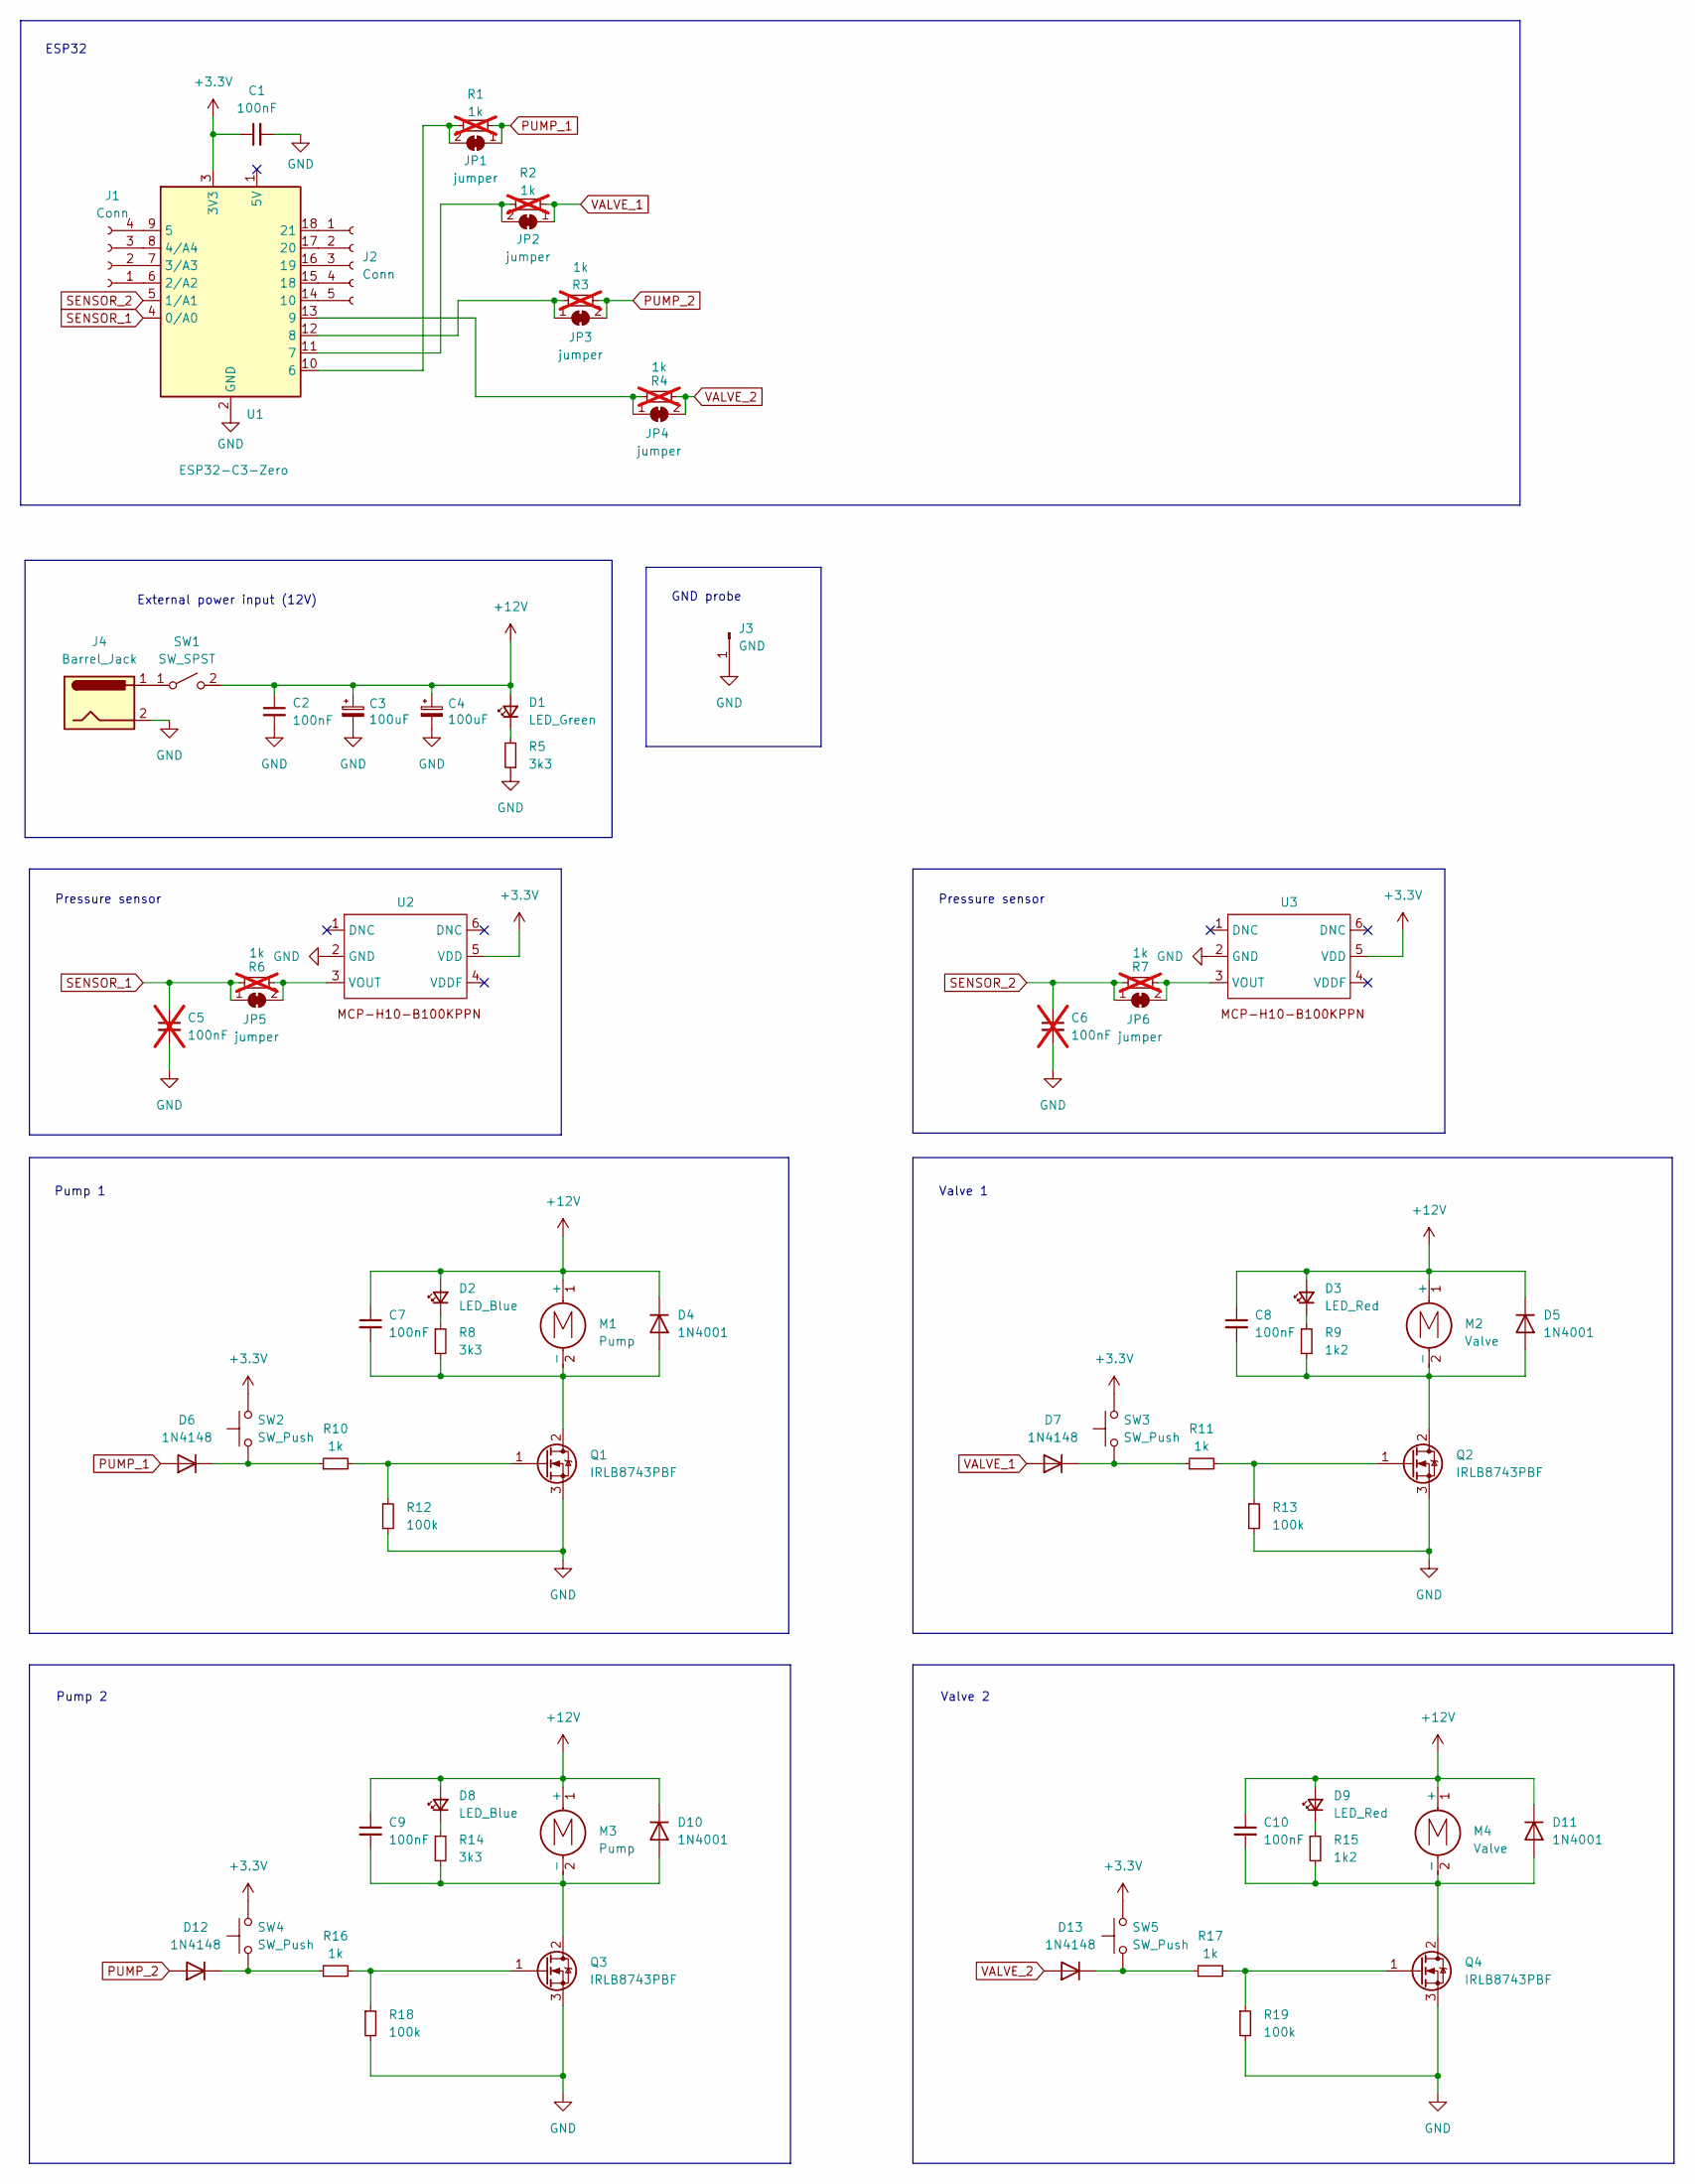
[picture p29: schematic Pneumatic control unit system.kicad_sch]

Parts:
C1, C2, C7, C8, C9, C10: 100nF; C_Rect_L7.2mm_W2.5mm_P5.00mm_FKS2_FKP2_MKS2_MKP2
C3, C4: 100uF; CP_Radial_D6.3mm_P2.50mm
C5, C6: 100nF; C_Rect_L7.2mm_W2.5mm_P5.00mm_FKS2_FKP2_MKS2_MKP2; not fitted
D1: LED_Green; LED_D3.0mm
D2, D8: LED_Blue; LED_D3.0mm
D3, D9: LED_Red; LED_D3.0mm
D4, D5, D10, D11: 1N4001; D_DO-41_SOD81_P10.16mm_Horizontal
D6, D7, D12, D13: 1N4148; D_DO-35_SOD27_P7.62mm_Horizontal
J1: Conn; PinSocket_1x04_P2.54mm_Vertical
J2: Conn; PinSocket_1x05_P2.54mm_Vertical
J3: GND; TestPoint_Loop_D2.50mm_Drill1.0mm
J4: Barrel_Jack; BarrelJack_Horizontal
JP1, JP2, JP3, JP4, JP5, JP6: jumper; SolderJumper-2_P1.3mm_Bridged_Pad1.0x1.5mm
M1, M3: Pump; TerminalBlock_Phoenix_MKDS-1,5-2_1x02_P5.00mm_Horizontal
M2, M4: Valve; TerminalBlock_Phoenix_MKDS-1,5-2_1x02_P5.00mm_Horizontal
Q1, Q2, Q3, Q4: IRLB8743PBF; TO-220-3_Vertical
R1, R2, R3, R4, R6, R7: 1k; R_Axial_DIN0207_L6.3mm_D2.5mm_P10.16mm_Horizontal; not fitted
R5, R8, R14: 3k3; R_Axial_DIN0207_L6.3mm_D2.5mm_P10.16mm_Horizontal
R9, R15: 1k2; R_Axial_DIN0207_L6.3mm_D2.5mm_P10.16mm_Horizontal
R10, R11, R16, R17: 1k; R_Axial_DIN0207_L6.3mm_D2.5mm_P10.16mm_Horizontal
R12, R13, R18, R19: 100k; R_Axial_DIN0207_L6.3mm_D2.5mm_P10.16mm_Horizontal
SW1: SW_SPST; SW_rocker_switch_small
SW2, SW3, SW4, SW5: SW_Push; SW_PUSH_6mm
U1: ESP32-C3-Zero
U2, U3: MCP_H10_breakout

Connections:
+3.3V: C1.1, SW2.2, SW3.2, SW4.2, SW5.2, U1.3 (3V3), U2.5 (VDD), U3.5 (VDD)
+12V: C2.1, C3.1, C4.1, C7.1, C8.1, C9.1, C10.1, D1.2 (A), D2.2 (A), D3.2 (A), D4.1 (K), D5.1 (K), D8.2 (A), D9.2 (A), D10.1 (K), D11.1 (K), M1.1 (+), M2.1 (+), M3.1 (+), M4.1 (+), SW1.2 (B)
GND: C1.2, C2.2, C3.2, C4.2, C5.2, C6.2, J3.1, J4.2, Q1.3 (S), Q2.3 (S), Q3.3 (S), Q4.3 (S), R5.1, R12.2, R13.2, R18.2, R19.2, U1.2 (GND), U2.2 (GND), U3.2 (GND); also elsewhere on the board
unnamed: D1.1 (K), R5.2
unnamed: D2.1 (K), R8.1
unnamed: D3.1 (K), R9.1
unnamed: C7.2, D4.2 (A), M1.2 (-), Q1.2 (D), R8.2
unnamed: C8.2, D5.2 (A), M2.2 (-), Q2.2 (D), R9.2
unnamed: D6.1 (K), R10.1, SW2.1
unnamed: D7.1 (K), R11.1, SW3.1
unnamed: D8.1 (K), R14.1
unnamed: D9.1 (K), R15.1
unnamed: C9.2, D10.2 (A), M3.2 (-), Q3.2 (D), R14.2
unnamed: C10.2, D11.2 (A), M4.2 (-), Q4.2 (D), R15.2
unnamed: D12.1 (K), R16.1, SW4.1
unnamed: D13.1 (K), R17.1, SW5.1
unnamed: J1.1, U1.6 (2/A2)
unnamed: J1.2, U1.7 (3/A3)
unnamed: J1.3, U1.8 (4/A4)
unnamed: J1.4, U1.9 (5)
unnamed: J2.1, U1.18 (21)
unnamed: J2.2, U1.17 (20)
unnamed: J2.3, U1.16 (19)
unnamed: J2.4, U1.15 (18)
unnamed: J2.5, U1.14 (10)
unnamed: JP1.2 (B), R1.1, U1.10 (6)
unnamed: JP2.2 (B), R2.1, U1.11 (7)
unnamed: JP3.1 (A), R3.2, U1.12 (8)
unnamed: JP4.1 (A), R4.2, U1.13 (9)
unnamed: JP5.2 (B), R6.1, U2.3 (VOUT)
unnamed: JP6.2 (B), R7.1, U3.3 (VOUT)
unnamed: Q1.1 (G), R10.2, R12.1
unnamed: Q2.1 (G), R11.2, R13.1
unnamed: Q3.1 (G), R16.2, R18.1
unnamed: Q4.1 (G), R17.2, R19.1
unnamed: J4.1, SW1.1 (A)
PUMP_1: D6.2 (A), JP1.1 (A), R1.2
PUMP_2: D12.2 (A), JP3.2 (B), R3.1
SENSOR_1: C5.1, JP5.1 (A), R6.2, U1.4 (0/A0)
SENSOR_2: C6.1, JP6.1 (A), R7.2, U1.5 (1/A1)
VALVE_1: D7.2 (A), JP2.1 (A), R2.2
VALVE_2: D13.2 (A), JP4.2 (B), R4.1

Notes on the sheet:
GND probe
Pressure sensor
Pump 2
External power input (12V)
Pump 1
Valve 1
ESP32
Valve 2

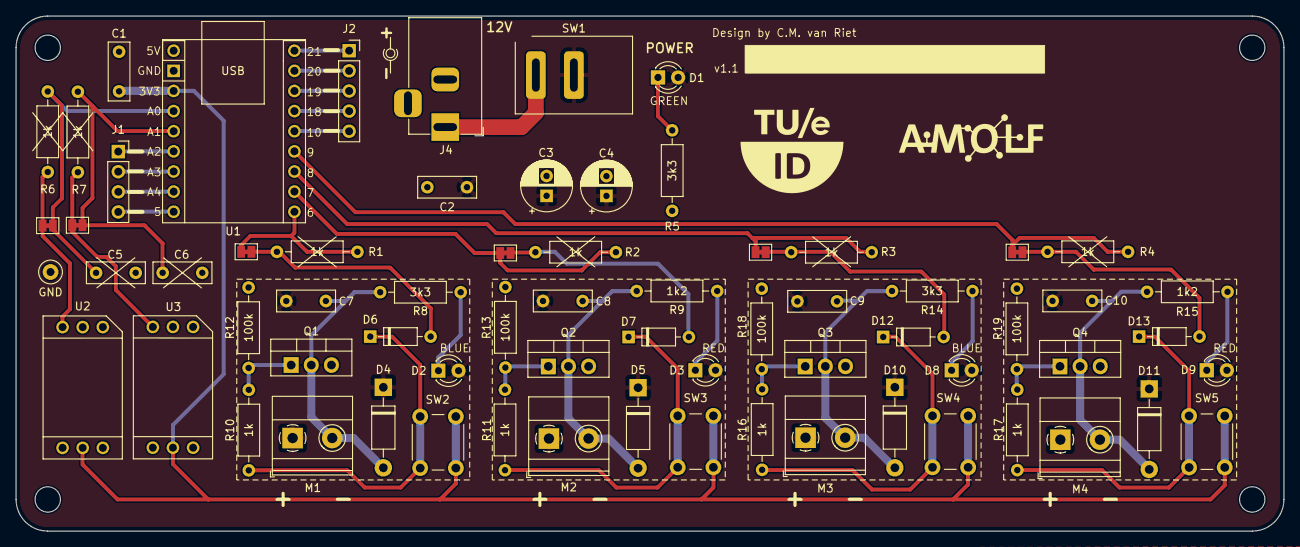
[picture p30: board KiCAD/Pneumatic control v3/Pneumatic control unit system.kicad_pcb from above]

Board: 2 copper layers, 160.0 x 65.0 mm, 68 parts (0 on the bottom side), 42 nets.

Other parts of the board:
GND: GND; TestPoint_Loop_D2.50mm_Drill1.0mm

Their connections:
GND: GND.1; also elsewhere on the board

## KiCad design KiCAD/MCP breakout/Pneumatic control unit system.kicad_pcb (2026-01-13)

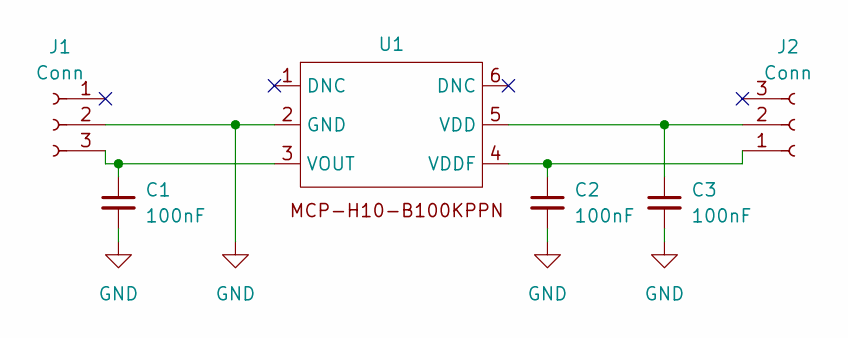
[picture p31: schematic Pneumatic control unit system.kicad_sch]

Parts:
C1, C2, C3: 100nF; C_0603_1608Metric_Pad1.08x0.95mm_HandSolder
J1, J2: Conn; PinHeader_1x03_P2.54mm_Vertical
U1: MCP-H10

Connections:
GND: C1.2, C2.2, C3.2, J1.2, U1.2 (GND)
unnamed: C1.1, J1.3, U1.3 (VOUT)
unnamed: C2.1, J2.1, U1.4 (VDDF)
unnamed: C3.1, J2.2, U1.5 (VDD)

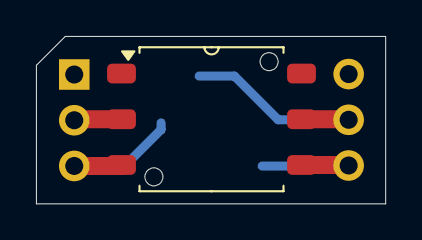
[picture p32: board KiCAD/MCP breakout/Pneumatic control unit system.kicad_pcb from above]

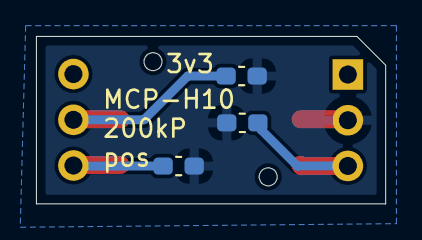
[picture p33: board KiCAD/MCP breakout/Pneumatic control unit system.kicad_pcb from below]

Board: 2 copper layers, 19.4 x 9.3 mm, 6 parts (5 on the bottom side), 4 nets.

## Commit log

2026-01-13 added overview board
2026-01-13 Added KiCAD and design files
    [Pneumatic control unit system BOM v2.csv, Pneumatic control unit system broad.step, Pneumatic control unit system follower.csv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]
2026-01-13 Updated print files
    [clamp big v5.stl, clamp small v5.stl, cushion connected v3.stl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]
2026-01-13 updated board overview pictures
2026-01-15 Create Air System manual soldering v1.0.pdf
2026-01-23 corrected valve control
    digitalWrite changed to analogWrite
